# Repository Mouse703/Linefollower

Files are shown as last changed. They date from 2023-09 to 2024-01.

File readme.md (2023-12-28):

# LineFollower Louis Van Roosmaelen

Plan A

## Specifications

**Microcontroller:** ESP32-WROOM NodeMCU (CP2102)

**Motors:** 2x 6VDC Motors 50:1 micro metal gearbox

**H-Bridge:** DollaTek DRV8833

**Sensors:** Pololu QTR-8A

**Batteries:** 2x XTAR 18650 (2200mAh, 5A, protected)

**Wireless Communication:** Telnet communication over WiFi (with optional web server)

**Distance Sensor - Motors:**
- Plan A: 107.5mm
- Plan B: 80mm

**Weight:**
- Plan A: 249 grams
- Plan B: 364 grams

**Speed:**
- Plan A: 0.633m/s
- Plan B: 0.446m/s

Plan A

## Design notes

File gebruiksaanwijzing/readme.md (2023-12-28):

# Gebruiksaanwijzing

## Opladen / Vervangen Batterijen
Het opladen van de batterijen gebeurt met de XTAR MC2 Plus lader. Plaats de batterijen in de houder met de juiste polariteit. Verbind de lader met je PC via een USB-kabel. Wanneer de 4 blauwe streepjes constant branden, zijn de batterijen opgeladen. Je kunt dit ook controleren met een multimeter; de volledig opgeladen spanning is 4,18V.

## Draadloze Communicatie
### Verbinding maken
Verbinding met de robot gebeurt via Telnet over WiFi. In het `config.h` bestand dien je de SSID en het wachtwoord van je netwerk in te vullen, alsook kan je best een hostname instellen voor je robot. Het WiFi netwerk kan zowel een thuisnetwerk als een hotspot zijn, maar het netwerk moet de 2.4GHz band ondersteunen. Dit komt omdat de ESP-32 van de robot alleen op 2.4GHz werkt. Ook moet je ervoor zorgen dat je op hetzelfde WiFi netwerk zit. Wanneer dit is ingevuld kan je de code uploaden naar de ESP-32 (zie handleiding).

Als je de robot met je PC wilt verbinden, hoef je geen extra software te installeren. Wel moet je een Windows-functie inschakelen door naar "Turn Windows features on or off" te gaan. Hier vind je de Telnet Client, die je moet aanvinken zodat de benodigde functies worden geïnstalleerd. 

Het ip adres kan je vinden door met een powershell terminal of command prompt een ping command te sturen. Dit kan gedaan worden met `ping -4 robot` (met robot als gekozen hostname) Je kan ook het ip address vinden in je hotspot-instellingen of door een USB-verbinding met de robot te maken en de seriële monitor te openen. Deze toont dan het IP adress / telnet poort waarmee de robot kan verbonden worden.

### 1: Powershell terminal (PC)
1. Zet de hotspot aan of verbind met hetzelfde WiFi-netwerk waar de ESP-32 zich op bevindt.
2. Open een powershell terminal met de toetsencombinatie `WIN` + `X` en selecteer Terminal.
3. Voer het commando telnet in met uw IP of hostname gevolgd door de telnet poort (bvb `telnet 192.168.137.239 2121`)
4. Nu wordt er automatisch een nieuwe window geopend en kan u commando's ingeven.

### 2: Mobile Telnet (smartphone app)
1. Zet de hotspot aan of verbind met hetzelfde WiFi-netwerk waar de ESP-32 zich op bevindt.
2. Open de app en klik rechtsboven op de 3 puntjes
3. Klik op telnet settings en voer het juiste IP address in met de bijhorende poort
4. Klik op connect en nu kan u commando's ingeven.

### Commando's
- `debug` Toont alle instelbare parameters
- `run (start/stop)` Start of stopt de robot
- `set cycle [µs]` Stelt de cyclustijd van de ESP-32 in
- `set power [0..255]` Stelt de kracht van de motoren in
- `set diff [0..1]` Stelt in hoe hard de robot moet bijsturen in de bochten (0 niets, 1 veel)
- `set kp [0..]` Stelt de proportionele correctie van de fout in (P-regeling)
- `set ki [0..]` Stelt de integrerende correctie van de fout in (I-regeling)
- `set kd [0..]` Stelt de differentiële correctie van de fout in (D-regeling)
- `set ledon` Zet de voor- en achterlichten aan
- `set ledred [0..255]` Stelt de helderheid van de rode lichten in
- `set ledorange [0..255]` Stelt de helderheid van de oranje lichten in
- `set ledwhite [0..255]` Stelt de helderheid van de witte lichten in
- `set ledstatus [0..255]` Stelt de helderheid van de statuslichten in
- `calibrate black` Kalibreert de zwartwaarden
- `calibrate white` Kalibreert de witwaarden

## Kalibratie
Kalibreer de zwartwaarden door de robot op een zwart oppervlak van het circuit te plaatsen en voer vervolgens het commando `calibrate black` in. Herhaal dit proces voor de witwaarden door de robot op een wit oppervlak van het circuit te plaatsen en het commando `calibrate white` in te voeren.

## Instellingen
De robot rijdt stabiel met de volgende parameters:
- **Cycle time**: 2500
- **Power**: 100
- **Diff**: 0.05
- **Kp**: 5
- **Ki**: 0
- **Kd**: 0

## Start/Stop-knop
De start/stop-knop bevindt zich naast de blauwe status-LED. Druk op deze knop om de running state van de robot te wijzigen, wat betekent dat de robot zal beginnen met rijden of stoppen, afhankelijk van de huidige toestand.

## Status LED's
Op de PCB bevinden zich status LED's. De brightness hiervan wordt ingesteld met `set ledstatus [0..255]`. De functie van deze LED's staan hieronder uitgelegd.
- **Blauwe LED** Bij knipperen: er wordt poging gedaan om met WiFi te verbinden. Bij vast licht: er is verbinding met een WiFi client. Bij geen licht: de WiFi verbinding is verbroken, robot moet herstart worden indien er weer parameters moeten aangepast worden.
- **Groene LED** Bij vast licht: de robot is klaar om te rijden maar in standby modus, er is een run command nodig of een druk op de startknop.
- **Oranje LED** Bij vast licht: de robot is aan het rijden.
- **Rode LED** Bij vast licht: de robot is buiten het parcour gegaan, er is een nieuwe run command nodig of een druk op de startknop.

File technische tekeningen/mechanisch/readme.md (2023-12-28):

# Mechanische Tekeningen

Dit is de verzameling mechanische tekeningen van het ontwerp, gemaakt met **Autodesk Inventor Professional 2024**. Hieronder vindt je ook de bronnen van alle geïmporteerde CAD modellen.

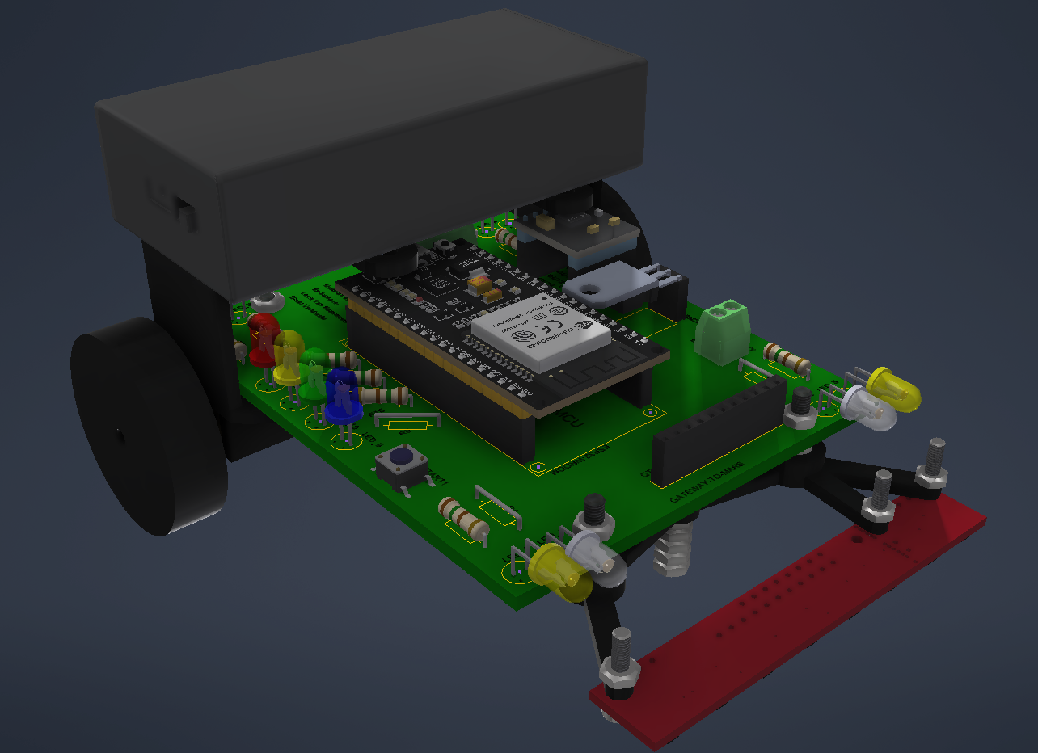
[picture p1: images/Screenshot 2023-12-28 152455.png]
3D Model - Plan A


## Source Imported CAD Files:

1. **Battery Holder 18650**
   - [Bekijk op GrabCAD](https://grabcad.com/library/3-7v-18650-2s-holder-1)

2. **DC Motor**
   - [Bekijk op GrabCAD](https://grabcad.com/library/dc-micro-metal-gearmotor-1)

3. **DRV 8833**
   - [Bekijk op GrabCAD](https://grabcad.com/library/drv8833-carrier-breakout-board-1)

4. **ESP32-WROOM-32S**
   - [Bekijk op GrabCAD](https://grabcad.com/library/esp32-wroom-32s-nodemcu-32s-1)

5. **Female Headers**
   - [Bekijk op GrabCAD](https://grabcad.com/library/arduino-female-pin-header-for-kicad-1)

6. **L7805CV**
   - [Bekijk op GrabCAD](https://grabcad.com/library/l7805-with-heat-sink-1)

7. **LED 5mm**
   - [Bekijk op GrabCAD](https://grabcad.com/library/led-5mm-0-2-inch-1)

8. **Pushbutton**
   - [Bekijk op GrabCAD](https://grabcad.com/library/pushbutton-switch-1)

9. **QTR-8A Reflectance Sensor Array**
   - [Bekijk op GrabCAD](https://grabcad.com/library/qtr-8a-reflectance-sensor-array-1)

10. **Resistor**
    - [Bekijk op GrabCAD](https://grabcad.com/library/resistors-0-5w-pitch-12-7mm-500mil-1)

11. **Screw Terminal**
    - [Bekijk op GrabCAD](https://grabcad.com/library/pcb-terminal-block-pitch-3-5mm-for-kicad-1)

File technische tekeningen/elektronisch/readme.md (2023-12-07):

# Electrical schematics

Schematics for plan A (using PCB) and plan B (using breadboard)

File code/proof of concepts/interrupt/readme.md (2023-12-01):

# Start/stop interrupt proof of concept
minimale hard- en software die de correcte werking van een start/stop drukknop aantoont, gebruik makend van een hardware interrupt

Interrupt_bb

ESP-32 WROOM used from:
https://github.com/Warlib1975/Fritzing-parts/blob/master/MH-ET%20LIVE%20ESP32%20DEVKIT%2038%20pins.fzpz

Interrupt_schem

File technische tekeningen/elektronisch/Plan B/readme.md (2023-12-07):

# Plan B - Breadboard
Plan B is the test phase of the line follower, everything gets mounted on a breadboard for easy testing. When test phase is complete plan A will be used.

Plan B - Schema_bb

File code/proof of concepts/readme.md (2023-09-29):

# Proof of Concepts

Een proof of concept is een combinatie van minimale hard- en software om eenvoudig aan te tonen dat iets werkt.  
Proof of concepts kunnen enerzijds als eerste poging dienen om een bepaald onderdeel van het project werkend te krijgen. Anderzijds kunnen ze tijdens het debuggen van het finale project dienen als test om eventuele hardware problemen te elimineren bij onduidelijke problemen.
<br />  
<br />
Een proof of concept bestaat uit
* een elektronisch schema (indien van toepassing)
* minimale code om de voorop gestelde zaken te demonstreren
* minimale uitleg / aandachtspunten
<br />
De elektronische schakelingen van de proof of concepts komen bij voorkeur overeen met deze van de uiteindelijke linefollower, zodat de code zonder aanpassingen op het finale project kan draaien.

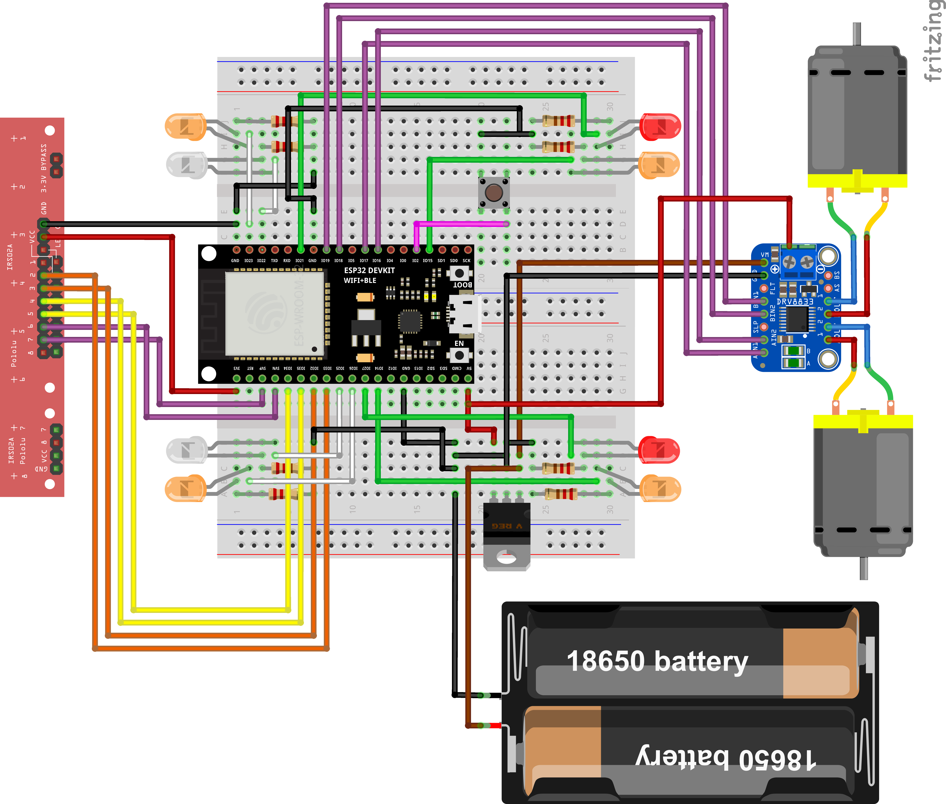
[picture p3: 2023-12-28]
technische tekeningen/mechanisch/Workingfolder - ELM3 - Project Synthese - LFR/Documents/Fritzing/Exports/Plan B - Schema_bb.png

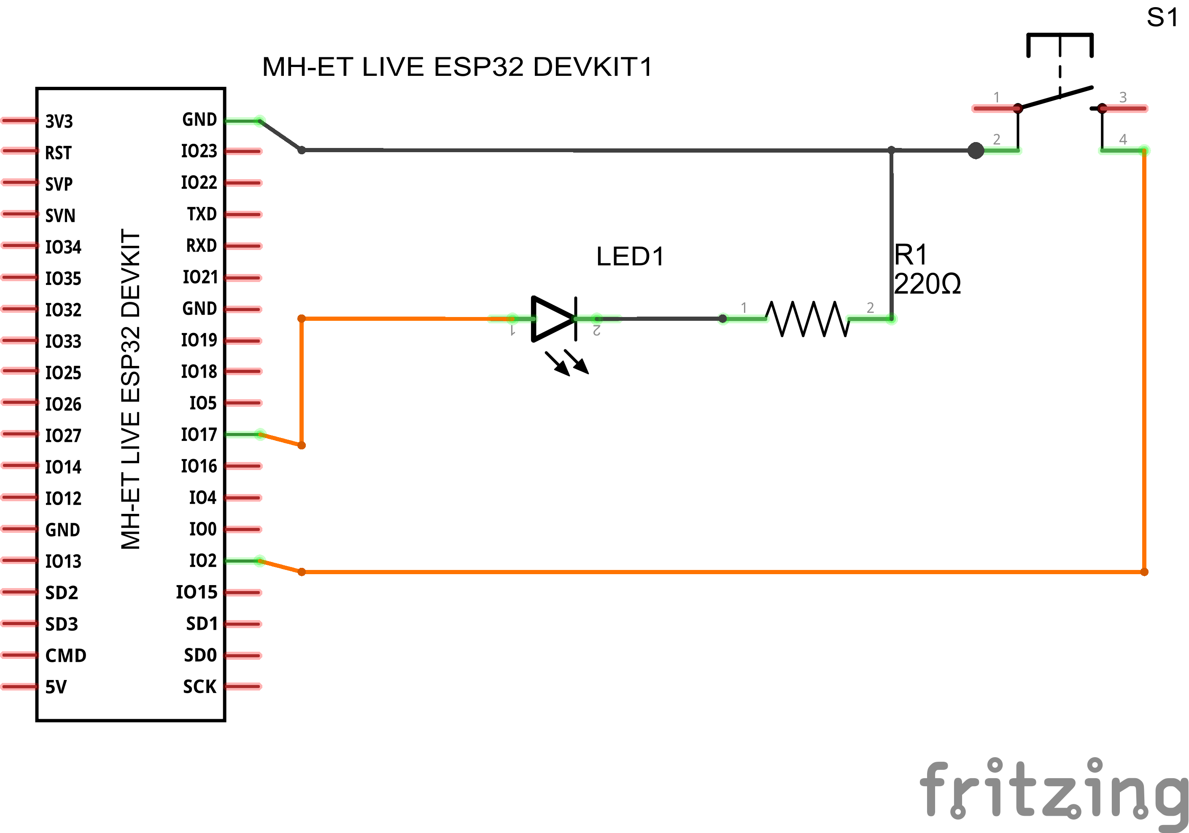
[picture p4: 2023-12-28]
technische tekeningen/mechanisch/Workingfolder - ELM3 - Project Synthese - LFR/Documents/Fritzing/Exports/Interrupt_schem.png

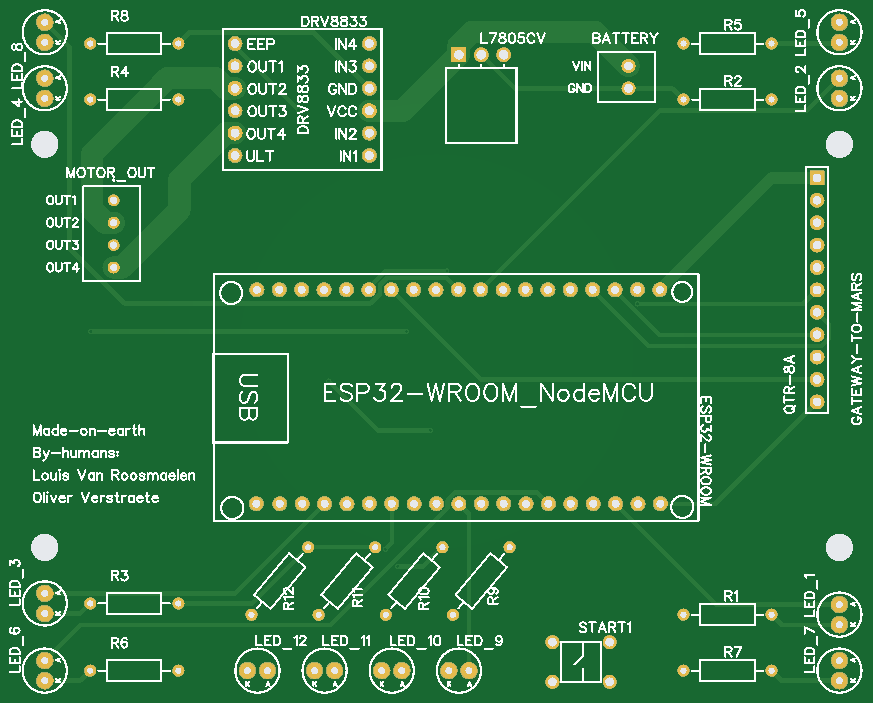
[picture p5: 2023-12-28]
technische tekeningen/mechanisch/Workingfolder - ELM3 - Project Synthese - LFR/Documents/PCB/PCB Preview.png

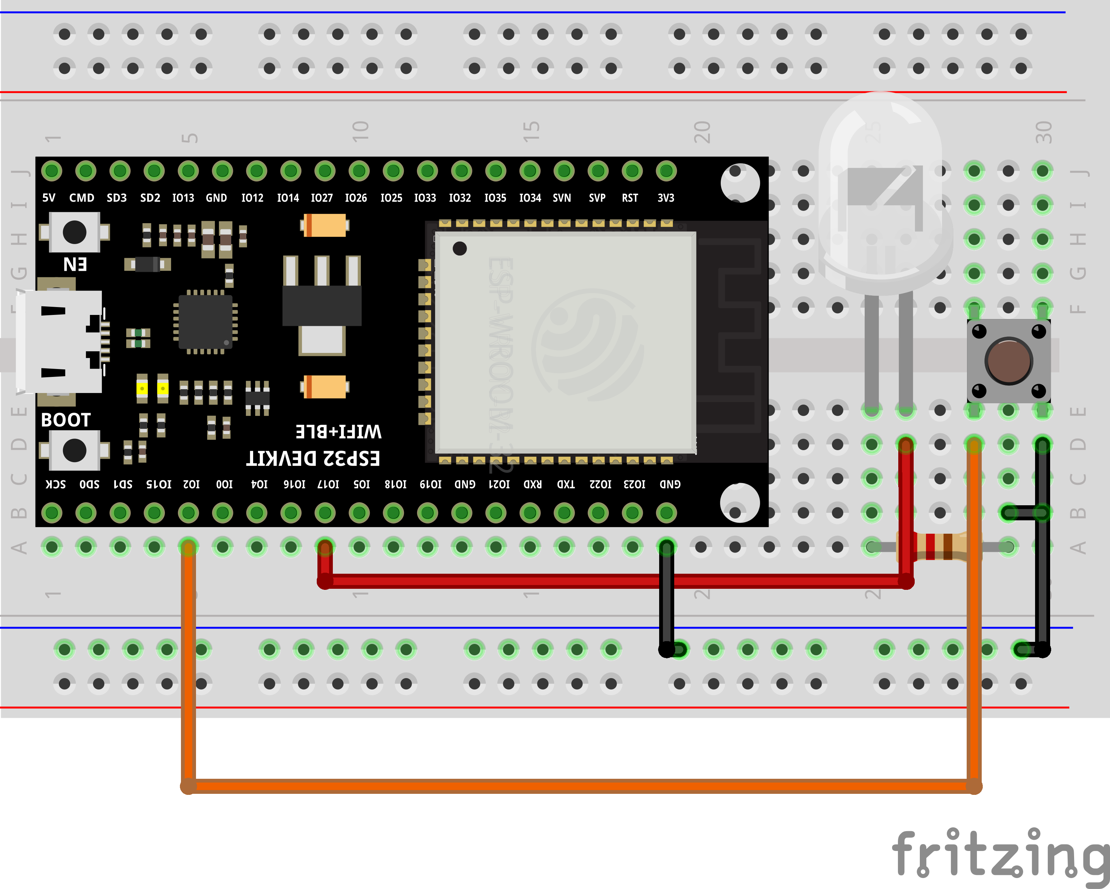
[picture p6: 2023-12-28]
technische tekeningen/mechanisch/Workingfolder - ELM3 - Project Synthese - LFR/Documents/Fritzing/Exports/Interrupt_bb.png

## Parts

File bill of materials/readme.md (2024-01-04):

## Bill of materials
<br />

|Volgnummer|Naam |Omschrijving |Nieuw/recup |Kostprijs/stuk|Aantal|Shipping|Subtotaal|
|---|---|---|---|---|---|---|---|
| 1| PA_Main |Behuizing (0,20mm NORMAL) |Ge-3D-print, Ender-3 V2 |0.93 |1 |0 |0.93 |
| 2| PA_Sensor |Vaste houder sensor 107.5mm (0,08mm SUPERDETAIL) |Ge-3D-print, Ender-3 V2 |0.05 |1 |0 |0.64 |
| 3| Pololu DC Micro Metal Gear 12V |50:1 ratio, 12VDC |Nieuw |10.56 |2 |9.99 |31.11 |
| 4| Batteries XTAR |XTAR 18650 (2200mAh, 5A, protected) |Nieuw |4.45 |2 |3.21 |12.11 |
| 5| Battery charger |XTAR MC1 Li-ion mini batterijlader |Nieuw |6.95 |1 |3.21 |10.16 |
| 6| Battery holder |2x18650 Batterijhouder met losse draden |Nieuw |0.96 |1 |1.46 |2.42 |
| 7| H-Bridge |DollaTek DRV8833 |Nieuw |1.90 |2 |1.46 |3.36 |
| 8| Reflectance sensor array |Polollulu QTR-8A |Nieuw |10.39 |1 |13.78 |24.17 |
| 9| Microcontroller ESP-32 |AZDelivery ESP32-WROOM-32 NodeMCU |Nieuw |7.60 |1 |0 |7.60 |
| 10| Wheels 40mm |Simulation rubber wheels 40mm |Nieuw |0.79 |2 |3.25 |4.04 |
| 11| PCB |PCB (aankoop min 5 stuks, taxen bij shipping) |Nieuw |1.11 |1 |22.03 |25.23 |
| 12| Tiny Tronics - PCB Component |4 Pin Schroef Terminal Block Connector 2.54mm |Nieuw |0.45 |1 |0 |0.45 |
| 13| Tiny Tronics - PCB Component |2 Pin Schroef Terminal Block Connector 2.54mm |Nieuw |0.30 |1 |0 |0.30 |
| 14| Tiny Tronics - PCB Component |20 Pins header Female |Nieuw |0.36 |2 |0 |0.72 |
| 15| Tiny Tronics - PCB Component |12 Pins header Female |Nieuw |0.28 |1 |0 |0.28 |
| 16| Tiny Tronics - PCB Component |6 Pins header Female |Nieuw |0.18 |2 |0 |0.36 |
| 17| Tiny Tronics - PCB Component |3 Pins header Female |Nieuw |0.12 |1 |0 |0.12 |
| 18| Tiny Tronics - PCB Component |6 Pins header Female |Nieuw |0.18 |2 |0 |0.36 |
| 19| Tiny Tronics - PCB Component |LED set 5mm - Groen - Rood - Geel - Blauw - Wit |Nieuw |3.00 |1 |0 |3.00 |
| 20| Tiny Tronics - PCB Component |10Ω-1MΩ Weerstanden Set |Nieuw |5.00 |1 |0 |5.00 |
| 21| Tiny Tronics - Shipping |Shipping |Nieuw |x |1 |7.95 |7.95 |
| 22| Countersunck crosshead screw |M3x12 |recup |x |9 |x |x |
| 23| DIN 912 |M2.5x18 |recup |x |3 |x |x |
| 24| DIN 985 |M2.5 |recup |x |3 |x |x |
| 25| Multi colour wires |0,75mm copper core wires |recup |x |x |x |x |
| 26| Pushbutton |Drukknop |recup |x |x |x |x |

Totaal zonder shipping: €73.69 

Totaal met shipping: €140.03

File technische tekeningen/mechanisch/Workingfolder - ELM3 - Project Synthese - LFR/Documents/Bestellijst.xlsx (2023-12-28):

Benodigdheden syntheseproject | Louis + Oliver + Roman
Onderdeel |  | Aantal | EPrijs | Kprijs | Verzending/BTW | Link
Motor | 50:1 Micro metal gearbox HP 6V | 6.00 | 2.04 | 12.24 | 3.22 | https://nl.aliexpress.com/item/33022320164.html?mp=1
Batterijen | XTAR 18650 2200mAh (protected) - 5A | 6.00 | 4.45 | 26.70 | 6.41 | https://www.nkon.nl/xtar-18650-2200mah-li-ion-battery.html
Batterijen oplader | XTAR MC1 Li-ion mini batterijlader | 3.00 | 6.95 | 20.85 | 0.00 | https://www.nkon.nl/charger-75/battery-charger/li-ion/xtar-mc2-plus-batterijlader.html
Batterijhouder | 2x 18650 Batterijhouder met losse draden | 3.00 | 0.32 | 0.96 | 2.92 | https://nl.aliexpress.com/item/32832812448.html?mp=1
H-brug | DollaTek 5 x DRV8833 | 1.00 | 5.47 | 5.47 | 0.00 | https://nl.aliexpress.com/item/1005006025943342.html?curPageLogUid=GeaIyxtrKBlw
Sensoren | QTR-8A Reflectance Sensor | 3.00 | 10.39 | 31.17 | 13.78 | https://www.melopero.com/shop/sensori/qtr8areflectancesensorarray/
Draadloze communicatie | Included (WiFi/Bluetooth) | 0.00 | 0.00 | 0.00 | 0.00 | n.v.t.
Microcontroller | AZDelivery ESP32 NodeMCU | 3.00 | 7.60 | 22.79 | 0.00 | https://www.amazon.com.be/-/nl/dp/B074RG86SR?psc=1&ref=ppx_yo2ov_dt_b_product_details
Wielen | Rubber wheel 40mm | 3.00 | 3.15 | 9.45 | 3.25 | https://nl.aliexpress.com/item/1005001687355617.html?curPageLogUid=2HmPvmFUd0g8
Breadboard | Breadbord 400mm | 6.00 | 1.02 | 6.12 | 5.03 | https://nl.aliexpress.com/item/32711841420.html?curPageLogUid=Gr2BDQawu44Q
Prijs totaal zonder shipping |  |  |  | 135.75
Totale shippingkosten en/of BTW |  |  |  | 34.61
Totale prijs |  |  |  | 170.36
Prijs per persoon (incl. shipping) |  |  |  | 56.79

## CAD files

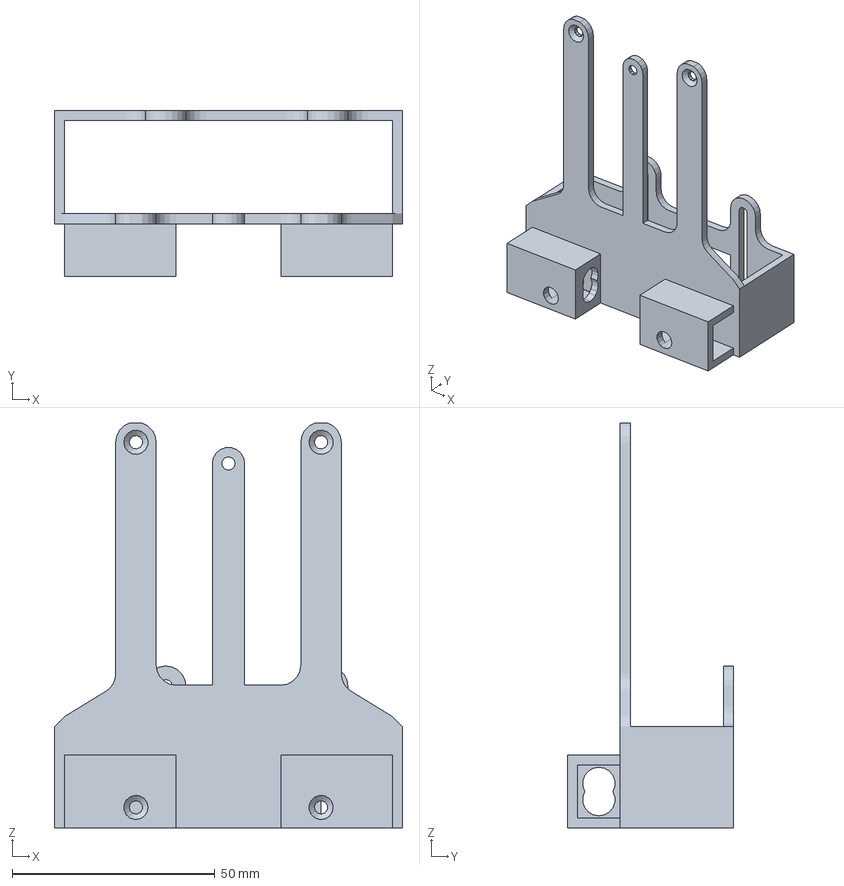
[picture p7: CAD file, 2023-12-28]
technische tekeningen/mechanisch/Workingfolder - ELM3 - Project Synthese - LFR/Engineering Data/PrusaSlicer/PA_Main.3mf
86.0 x 41.0 x 100.0 mm

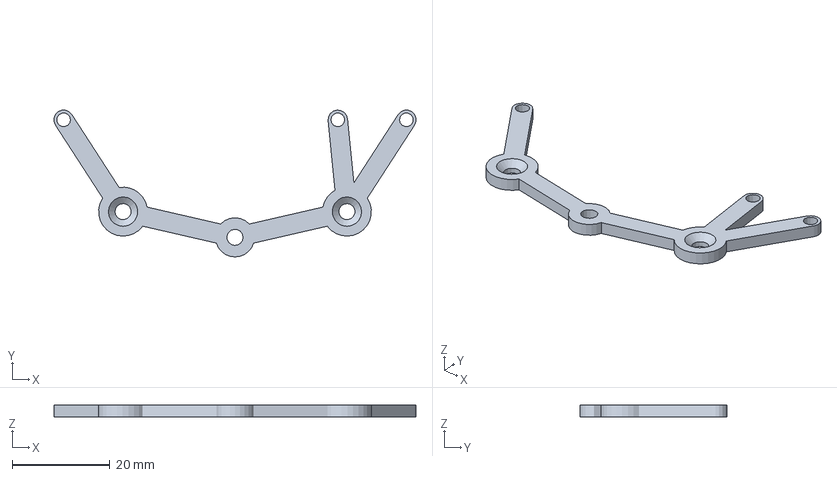
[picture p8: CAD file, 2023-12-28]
technische tekeningen/mechanisch/Workingfolder - ELM3 - Project Synthese - LFR/Engineering Data/PrusaSlicer/PA_Sensor.3mf
73.9 x 30.0 x 2.40 mm

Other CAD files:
technische tekeningen/mechanisch/Workingfolder - ELM3 - Project Synthese - LFR/Engineering Data/STL/PA_Main.stl
technische tekeningen/mechanisch/Workingfolder - ELM3 - Project Synthese - LFR/Engineering Data/STL/PA_Sensor.stl
technische tekeningen/mechanisch/Workingfolder - ELM3 - Project Synthese - LFR/Content Center/en-US/DIN 125-1 A/DIN 125 - A 4.3.ipt
technische tekeningen/mechanisch/Workingfolder - ELM3 - Project Synthese - LFR/Content Center/en-US/DIN 912/DIN 912 - M2.5 x 0.45 x 12 x 10.875.ipt
technische tekeningen/mechanisch/Workingfolder - ELM3 - Project Synthese - LFR/Content Center/en-US/DIN 912/DIN 912 - M4 x 0.7 x 16 x 14.25.ipt
technische tekeningen/mechanisch/Workingfolder - ELM3 - Project Synthese - LFR/Content Center/en-US/DIN 912/DIN 912 - M4 x 0.7 x 20 x 18.25.ipt
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

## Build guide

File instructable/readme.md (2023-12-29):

# Instructible

## Inhoudsopgave
1. [Bestellen van Componenten](#stap-1-bestellen-van-componenten)
2. [3D-printen](#stap-2-3d-printen)
3. [Tools en Overzicht](#stap-3-tools-en-overzicht)
4. [Elektrische Montage op PCB (Headers)](#stap-4-elektrische-montage-op-pcb-headers)
5. [Elektrische Montage op PCB (Weerstanden)](#stap-5-elektrische-montage-op-pcb-weerstanden)
6. [Elektrische Montage op PCB (LED’s)](#stap-6-elektrische-montage-op-pcb-leds)
7. [Montage Sensorhouder op het Chassis](#stap-7-montage-sensorhouder-op-het-chassis)
8. [Monteren PCB op het Chassis](#stap-8-monteren-pcb-op-het-chassis)
9. [Elektrische Montage QTR-8A](#stap-9-elektrische-montage-qtr-8a)
10. [Monteren QTR-8A op Chassis en Verbinding met PCB](#stap-10-monteren-qtr-8a-op-chassis-en-verbinding-met-pcb)
11. [Monteren van de Motoren](#stap-11-monteren-van-de-motoren)
12. [Monteren Batterijhouder en Spanningsverdeler](#stap-12-monteren-batterijhouder-en-spanningsverdeler)
13. [Installeren Visual Studio Code](#stap-13-installeren-visual-studio-code)
14. [Installeren Platform.io](#stap-14-installeren-platformio)
15. [Openen project](#stap-15-openen-project)
16. [Installeren driver voor ESP32](#stap-16-installeren-driver-voor-esp32)
17. [Parameters UserConfig.h](#stap-17-parameters-userconfigh)
18. [Uploaden naar ESP32](#stap-18-uploaden-naar-esp32)
19. [Batterijen plaatsen](#stap-19-batterijen-plaatsen)
20. [Robot starten](#stap-20-robot-starten)

---

## Stap 1: Bestellen van Componenten
In de [Bill of Materials](../bill%20of%20materials) (BOM) vindt u de benodigde componenten, die verkrijgbaar zijn bij de bijbehorende link. Als de link niet meer werkt, kunt u altijd ook een vervangende zoeken op Amazon of AliExpress. Het is handig om van elk onderdeel ten minste twee exemplaren te kopen, waardoor u bij eventuele defecten direct een vervangend exemplaar paraat heeft.

## Stap 2: 3D-printen
Er zijn diverse methoden beschikbaar om de onderdelen te 3D printen. Indien u in het bezit bent van een Ender-3 V2, kunt u eenvoudig de [.gcode](../technische%20tekeningen/mechanisch/GCODE) bestanden uploaden naar een SD-kaart en direct aan de slag gaan met printen (gebruikmakend van PLA, extruder ingesteld op 200°C en het printbed op 60°C). Wil je de printerinstellingen nakijken of aanpassen, dan kunt u de [.3mf](../technische%20tekeningen/mechanisch/PrusaSlicer) bestanden openen in PrusaSlicer. Voor degenen die de voorkeur geven aan andere software, is het ook mogelijk om de [.stl](../technische%20tekeningen/mechanisch/STL) bestanden te importeren. Als u wijzigingen wilt aanbrengen in het 3D-design, kunt u de originele [originele bestanden](../technische%20tekeningen/mechanisch/Workingfolder%20-%20ELM3%20-%20Project%20Synthese%20-%20LFR) openen met Autodesk Inventor. Het is van belang om alles te downloaden binnen deze map, zodat Inventor alle benodigde referenties kan vinden.

## Stap 3: Tools en Overzicht
Zorg voor een workspace dat goed en gestructureerd is, dit voorkomt het verliezen van componenten. Voor tools hebt u het volgende nodig:
1. Toolbox met inbussleutels, dopsleutels en schroevendraaiers.
2. Een kniptang en striptang.
3. Breekmes, schuifmaat en dubbelzijdige plakband zijn ook handig.
4. Soldeerstation met de bijbehorende tin.

## Stap 4: Elektrische Montage op PCB (Headers)
Neem de volgende componenten erbij:
- PCB
- 1x 2-pin schroef terminal block
- 1x 4-pin schroef terminal block
- 1x 3-pin header female
- 2x 6-pin header female
- 1x 12-pin header female
- 2x 20-pin header female

We knippen van de 20 pin female headers 1 pin eraf zodat dit een 19 pin header wordt, deze past dan in de PCB. Vervolgens doen we hetzelfde voor de 12 pin female header, zodat deze een 11 pin header wordt. Soldeer nu de componenten aan de PCB zoals te zien op onderstaande foto.



## Stap 5: Elektrische Montage op PCB (Weerstanden)
Neem nu 9 weerstanden van 150Ω. Soldeer deze op de aangegeven locaties op het PCB, namelijk R3, R4, R5, R6, R7, R8, R10, R11 en R12. Voor R1, R2 en R9 hoeft geen weerstand te worden geplaatst; in plaats daarvan kan je restanten van andere gebruiken om de weerstanden te overbruggen. Dit komt doordat de blauwe en witte LED's, volgens de informatie op de website van de verkoper (TinyTronics), geen voorschakelweerstand nodig hebben. Als u andere LED's hebt gekocht, is het mogelijk dat ze wel een voorschakelweerstand nodig hebben, en in dat geval kunt u deze op die posities plaatsen.



## Stap 6: Elektrische Montage op PCB (LED’s)
Neem nu de volgende componenten erbij:
- 1x blauwe LED
- 1x groene LED
- 2x witte LED’s
- 3x rode LED’s
- Pushbutton
- ESP32-WROOM-32
- DRV8833

Soldeer de LED’s op de juiste plaats. Soldeer witte LED’s op LED_1 en LED_2. Voor LED_3, LED_4 en LED_12 soldeer je rode LED's. Op LED_5, LED_6, LED_7, LED_8 en LED_11 soldeer je oranje LED's. Op LED_10 komt een groene LED en ten slotte op LED_9 soldeer je een blauwe LED. Neem een pushbutton erbij en soldeer deze op de aangewezen plaats genaamd START1. Vervolgens nemen we de DRV8833 en solderen we de male headers met de korte pinnen aan de bovenkant zoals op de foto te zien is. Ten slotte plaatsen we de ESP-32 op de headers met de usb poort naar de achterkant, zoals het diagram op de PCB aantoont.



## Stap 7: Montage Sensorhouder op het Chassis
Neem het ge-3d-printe chassis en de ge-3d-printe sensorhouder. Deze worden verbonden met elkaar door middel van M3x16 en M3x10 bouten. Plaats de bouten zoals op de foto en bevestig de moeren. De twee achterste bouten bij de motor moeten M3x10 zijn, terwijl de drie voorste bouten bij de sensorhouder M3x16 moeten zijn.



## Stap 8: Monteren PCB op het Chassis
Neem het chassis en plaats de PCB over de 4 bouten die naar boven uitsteken. Neem dan 4 bouten en bevestig de PCB aan het chassis.



## Stap 9: Elektrische Montage QTR-8A
Neem de volgende componenten erbij:
- QTR-8A
- Krimpkous (⌀2,5)
- Kabels vaste kern (0,8mm²)

Neem de QTR-8A sensor en soldeer de mannelijke headers op de sensor volgens de afbeelding. Vervolgens gebruik je enkele kabels van ongeveer 6 cm. Soldeer deze kabels aan de mannelijke headers en schuif de krimpkous over de kabels, zoals te zien is op de foto. Verwarm ten slotte de krimpkous met een haardroger of lucifer.

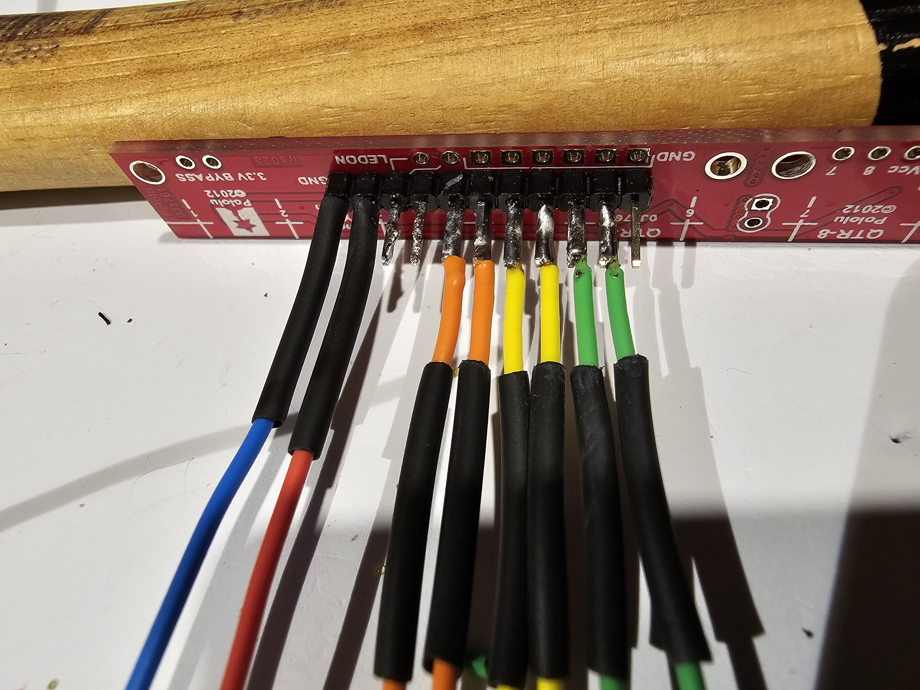
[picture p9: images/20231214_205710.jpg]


## Stap 10: Monteren QTR-8A op Chassis en Verbinding met PCB
Bevestig de QTR-8A sensor aan het chassis volgens de afbeelding. Hiervoor zijn 3 M2,5x12 bouten en 3 M2,5 moeren nodig. Zodra de sensor is bevestigd, kunt u de draden aansluiten zoals aangegeven door de paden op de PCB. De GND bevindt zich helemaal links, terwijl de VCC helemaal rechts bij de bout zit. Als je niet zeker bent, kun je de traces op de PCB volgen om te zien waar ze naartoe leiden.



## Stap 11: Monteren van de Motoren
Neem de twee DC-motoren en voorzie ze elk van twee kabels: een rode voor de positieve zijde (+) en een blauwe voor de negatieve zijde (-). Plaats vervolgens de motoren met de kabels eerst in de houder. Bevestig da

## Stap 12: Monteren Batterijhouder en Spanningsverdeler
Neem de volgende componenten erbij:
- Batterijhouder
- 2x M3x10 bouten
- 2x M3 moeren
- 2x kabels vaste kern (0,8mm²)
- Krimpkous
- Spanningsverdeler (L7805CV)

Eerst gaan we de uiteinden van de batterijhouder voorzien van een draad met een vaste kern. Dit maakt het gemakkelijker om ze te verbinden met de schroefterminal van de PCB. Soldeer de rode draad van de batterijhouder aan een draad met een vaste kern en plaats er een stukje krimpkous over. Verwarm de krimpkous en herhaal dit proces voor de andere draad van de batterijhouder. Plaats vervolgens de draden in de juiste polariteit (bruin/rood naar VIN en zwart/blauw naar GND) in de schroefterminal. Bevestig de batterijhouder met M3-bouten en moeren zoals weergegeven in de foto. Ten slotte bevestigen we de spanningsverdeler (L7805CV) aan de PCB. Zorg ervoor dat de zijde met de heat spreader naar boven wijst, omdat de polariteit correct moet zijn. Bij twijfel kun je altijd de datasheet en het elektrisch schema raadplegen.



## Stap 13: Installeren Visual Studio Code
Om het correcte programma te uploaden naar onze ESP32 moeten we Visual Studio Code installeren. Dit kan heel simpel gedaan worden door een powershell terminal te openen en volgend commmando in te geven `winget install -e --id Microsoft.VisualStudioCode`

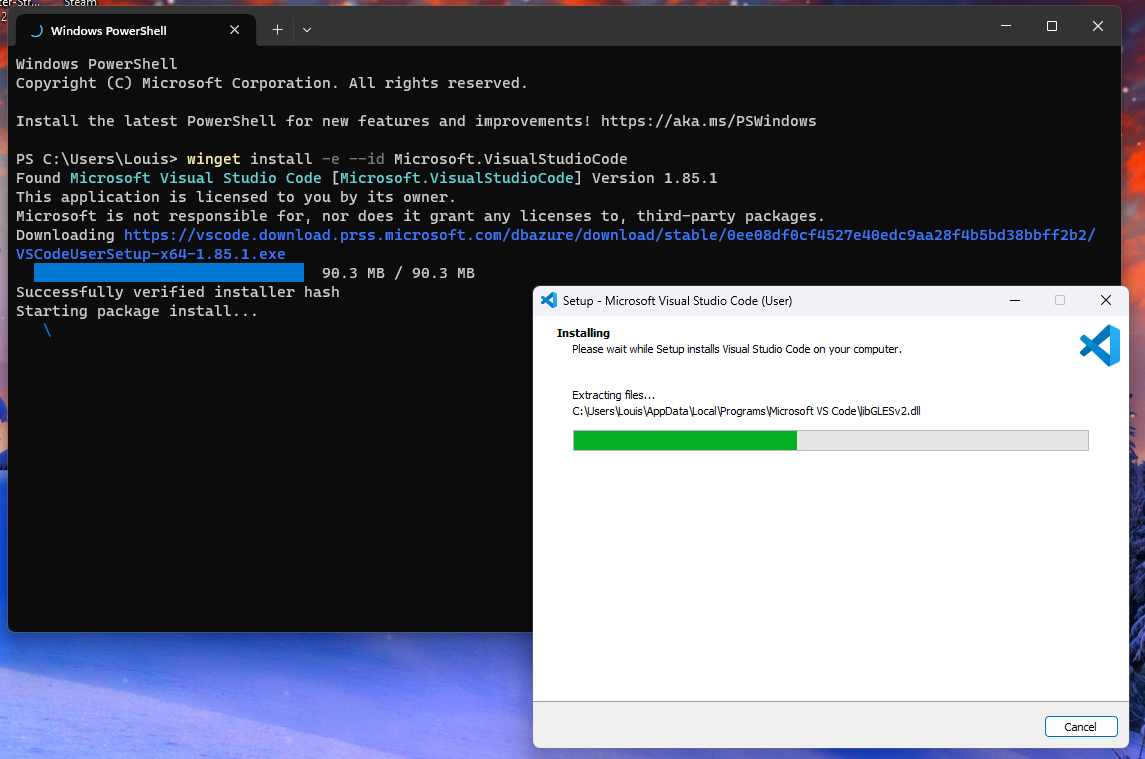
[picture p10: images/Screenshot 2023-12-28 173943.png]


## Stap 14: Installeren Platform.io
Nu moeten we een IDE installeren in Visual Studio zodat we gemakkelijk kunnen uploaden. Dit doen we door naar extensions te gaan in visual studio code, dan te zoeken naar PlatformIO IDE en deze te installeren.

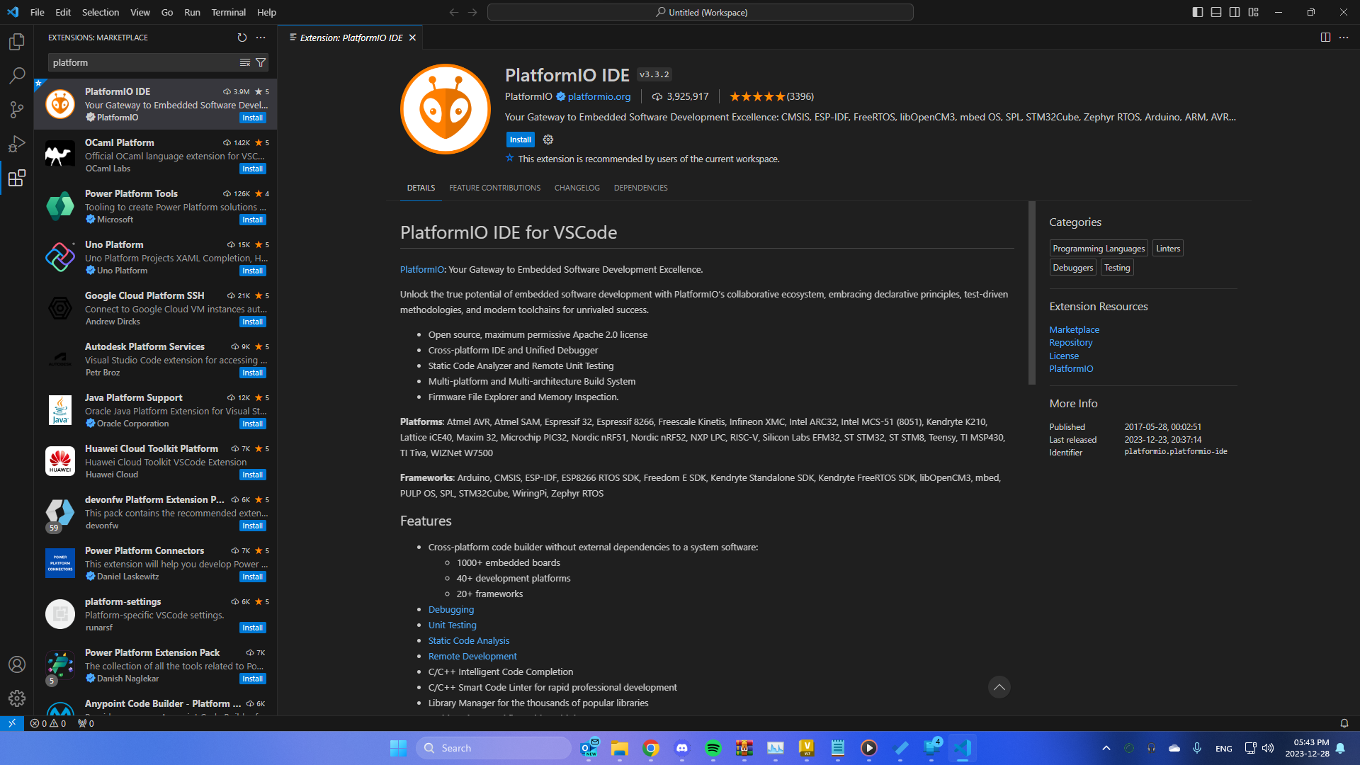
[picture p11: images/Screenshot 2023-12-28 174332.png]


## Stap 15: Openen project
Om het project te openen in platform.io gaan we naar PIO Home -> Open -> Open Project. [Het project vind je hier (download de map Syntheseproject - Code)](../code/finaal/) 

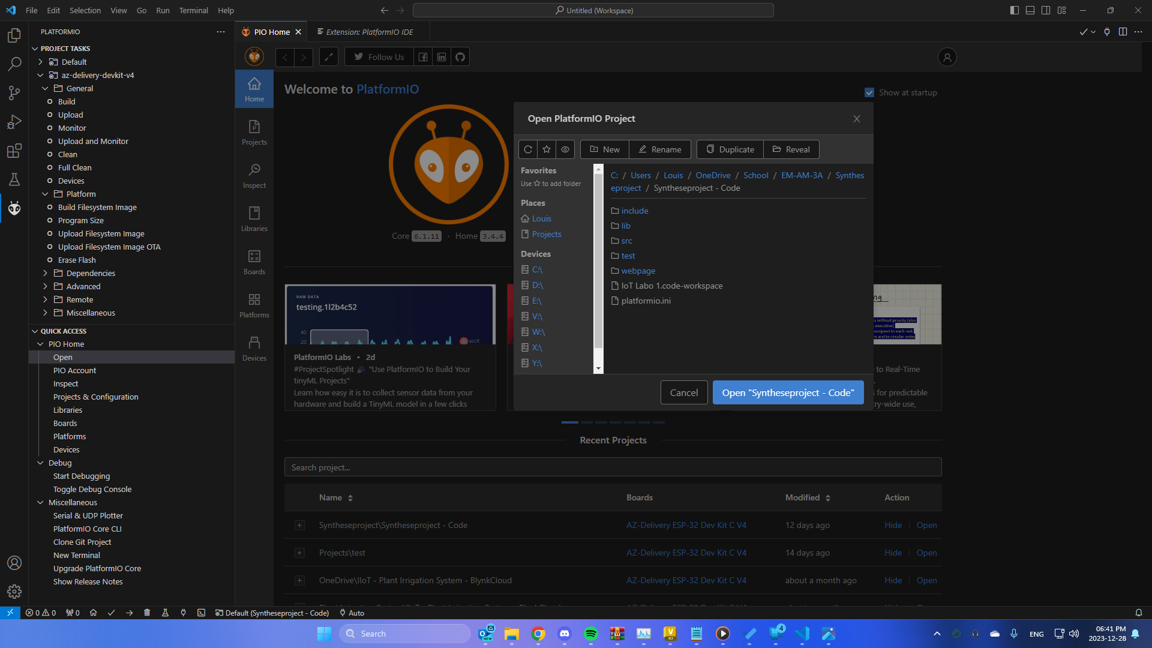
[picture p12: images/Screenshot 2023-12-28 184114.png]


## Stap 16: Installeren driver voor ESP32
Verbind nu de ESP32 met de computer, OPGELET, indien de batterijen van de robot al in de houder zitten dan moeten die UIT staan, als dit niet gedaan wordt zal je 8,4V op de USB poort terugsturen wat permanente schade kan toebrengen. De ESP32 zal nu nog niet herkend worden op de computer, eerst moeten we een driver installeren. [Deze driver (CP210x) je hier vinden.](../code/finaal/) Ga dan naar `apparaatbeheer` of `device manager` (te vinden in controlepaneel) op je computer. Bij `overige apparaten` of `other devices` zie je nu staan `CP2102 USB to UART Bridge Controller` met een warning sign. Rechtermuisklik op het apparaat en klik op update driver. Selecteer dan `Browse my computer for drivers` en ga naar de map waar je de CP210x driver hebt gedownload. Klik dan op next en dan op close wanneer alles geupdate is.

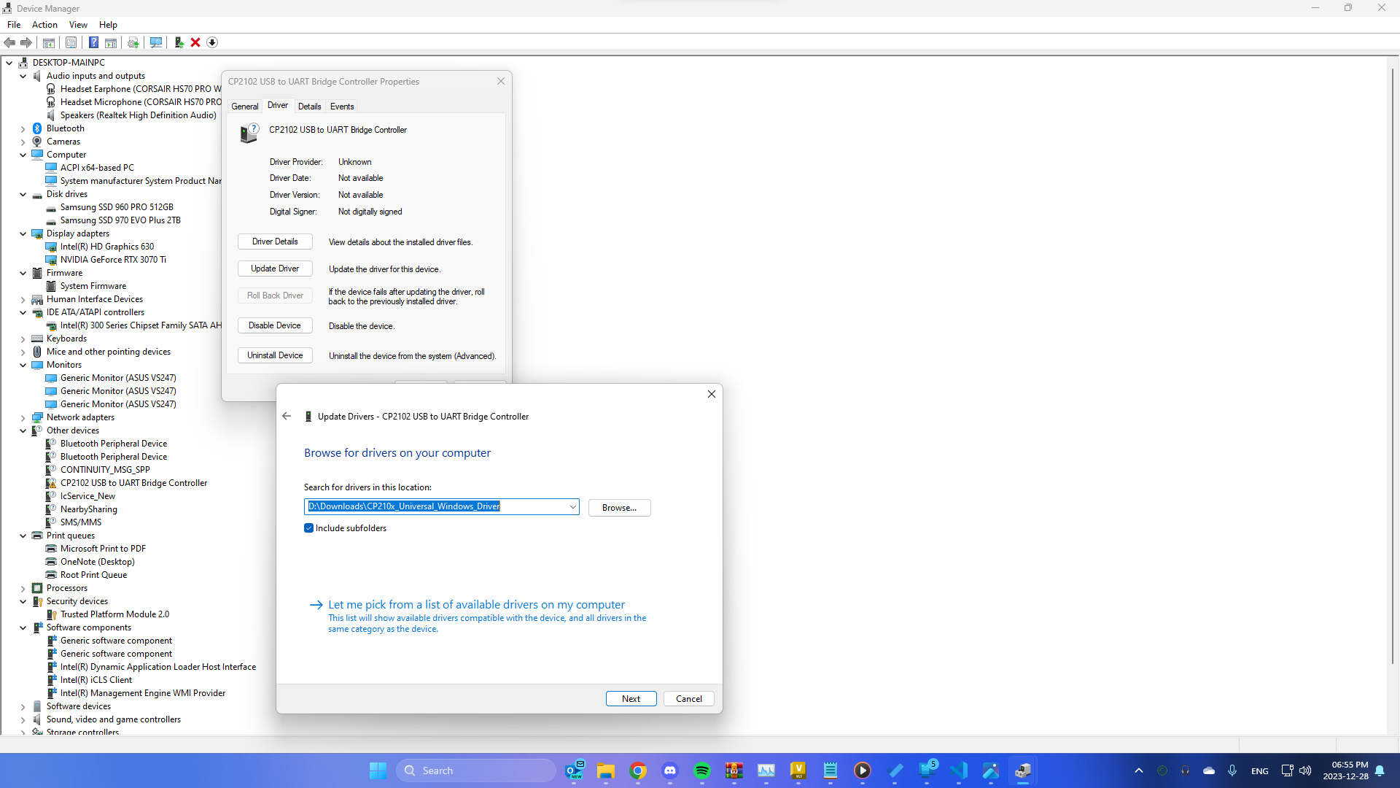
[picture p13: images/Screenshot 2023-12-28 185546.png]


## Stap 17: Parameters UserConfig.h
Ga nu terug naar Visual Studio. In de explorer van visualstudio klap je nu `src` open, daarin staan twee bestanden, `main.cpp` en `UserConfig.h`. Open `UserConfig.h` en stel uw eigen parameters in. `ssid` is de netwerknaam van uw netwerk, `pswd` is het passwoord van uw netwerk en `host` is om gemakkelijk uw device terug te vinden op uw netwerk.

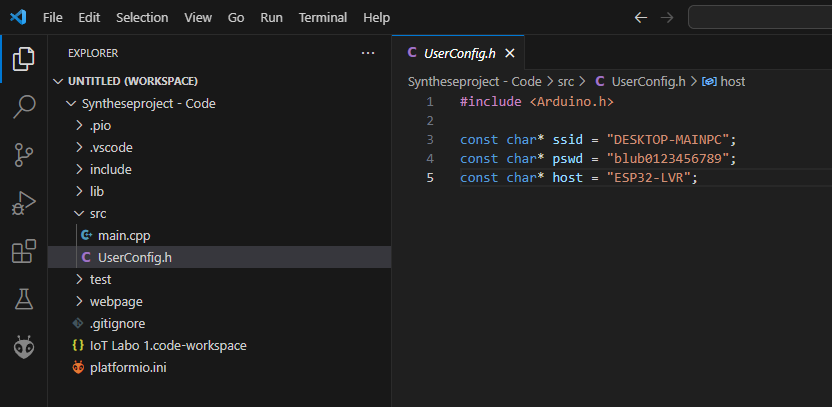
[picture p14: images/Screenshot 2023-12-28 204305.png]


## Stap 18: Uploaden naar ESP32
Klik nu op upload dat je kan vinden in de balk linksonder, het ziet eruit als een pijltje. Wanneer dit succesvol gedaan is zie je in de terminal `SUCCES` in het groen verschijnen.

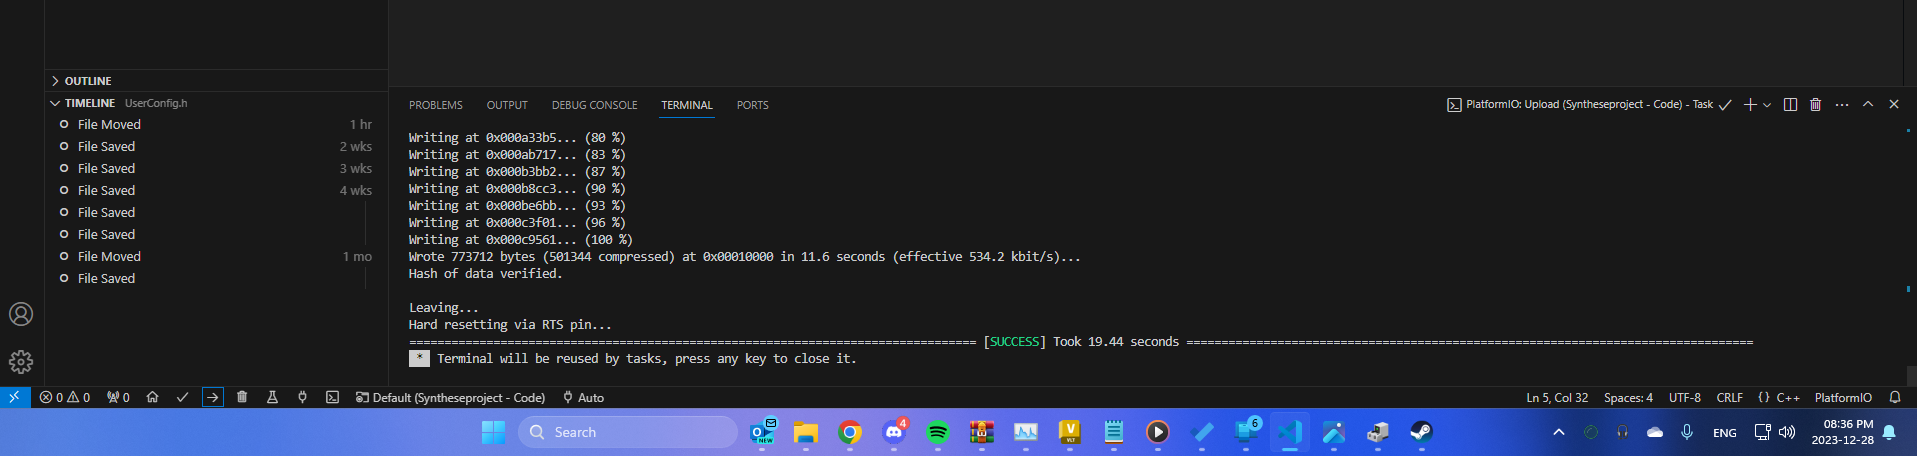
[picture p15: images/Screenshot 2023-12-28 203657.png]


## Stap 19: Batterijen plaatsen
Nu is alles klaar om de robot zijn eigen voeding te geven. Verbreek de verbinding met de PC en haal de USB kabel eruit. Plaats de twee XTAR batterijen in de houder en zet de switch in de ON positie.



## Stap 20: Robot starten
Maak verbinding met de robot en geef de stabiele waardes in. Meet uitleg hierover kan u vinden in de [manual.](../gebruiksaanwijzing/readme.md) Druk vervolgens op de startknop, vanaf nu kan je de waardes aanpassen om zoveel mogelijk snelheid te halen. Veel succes!



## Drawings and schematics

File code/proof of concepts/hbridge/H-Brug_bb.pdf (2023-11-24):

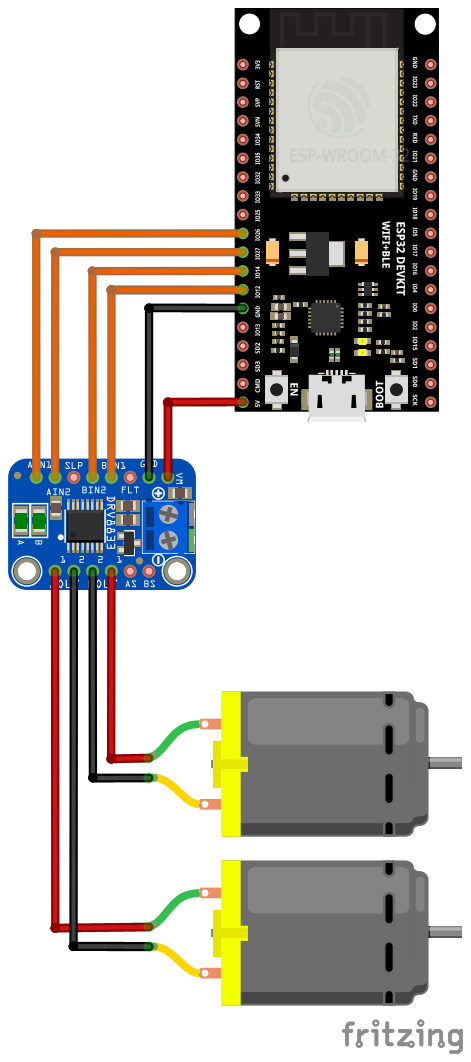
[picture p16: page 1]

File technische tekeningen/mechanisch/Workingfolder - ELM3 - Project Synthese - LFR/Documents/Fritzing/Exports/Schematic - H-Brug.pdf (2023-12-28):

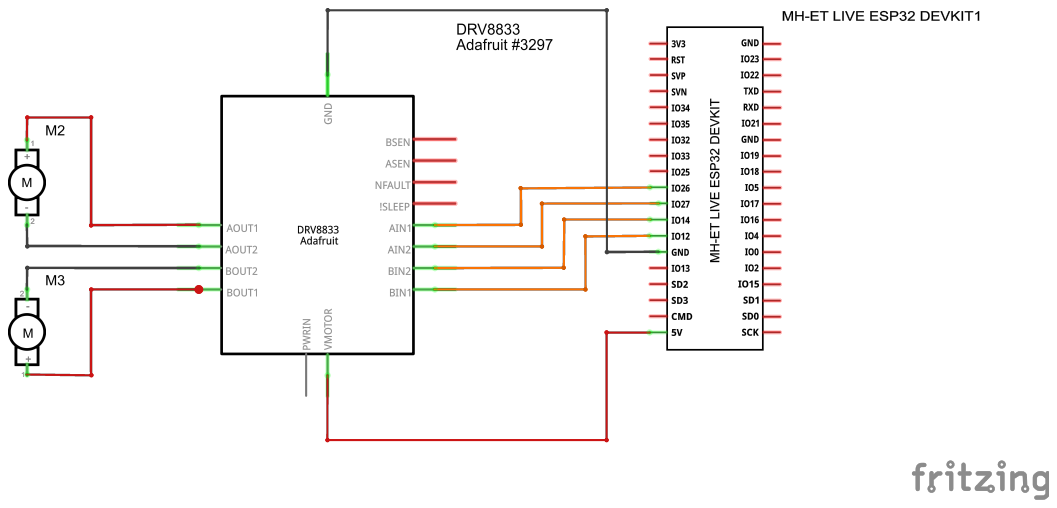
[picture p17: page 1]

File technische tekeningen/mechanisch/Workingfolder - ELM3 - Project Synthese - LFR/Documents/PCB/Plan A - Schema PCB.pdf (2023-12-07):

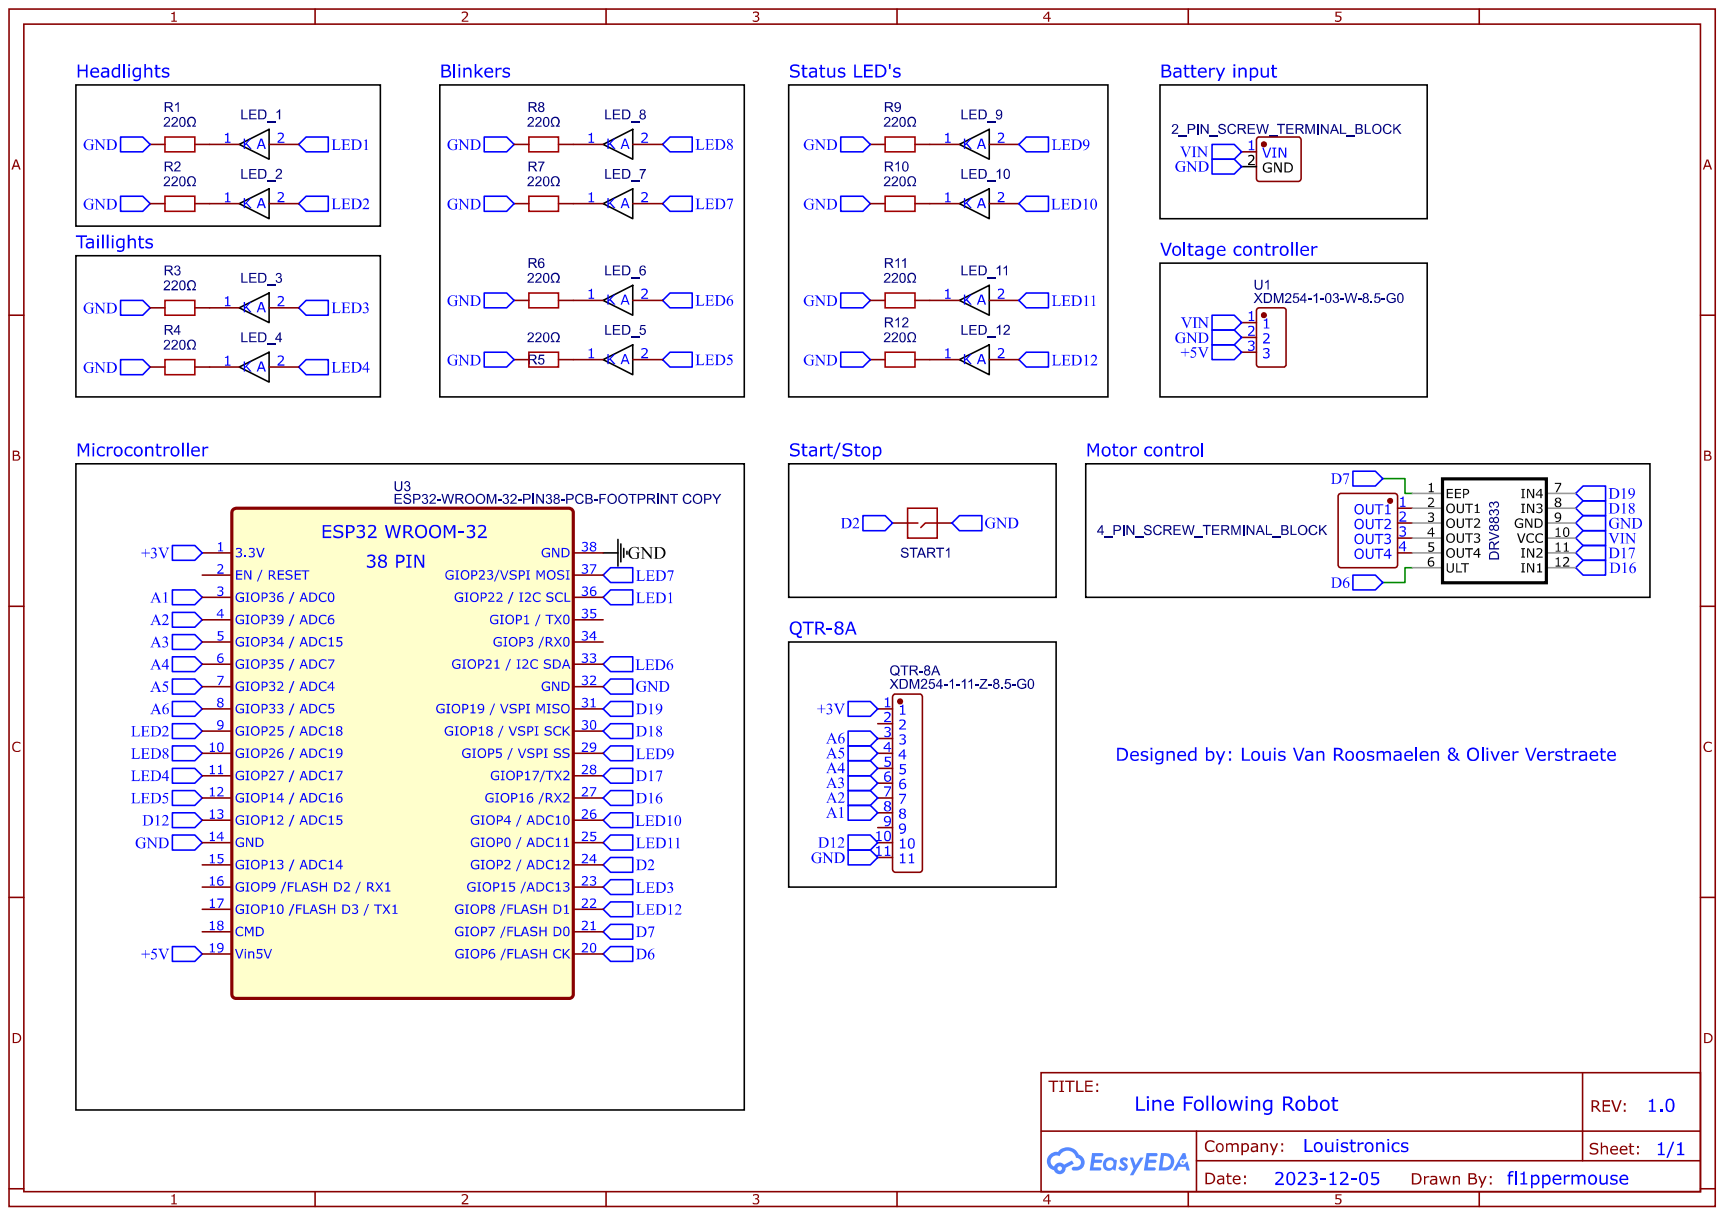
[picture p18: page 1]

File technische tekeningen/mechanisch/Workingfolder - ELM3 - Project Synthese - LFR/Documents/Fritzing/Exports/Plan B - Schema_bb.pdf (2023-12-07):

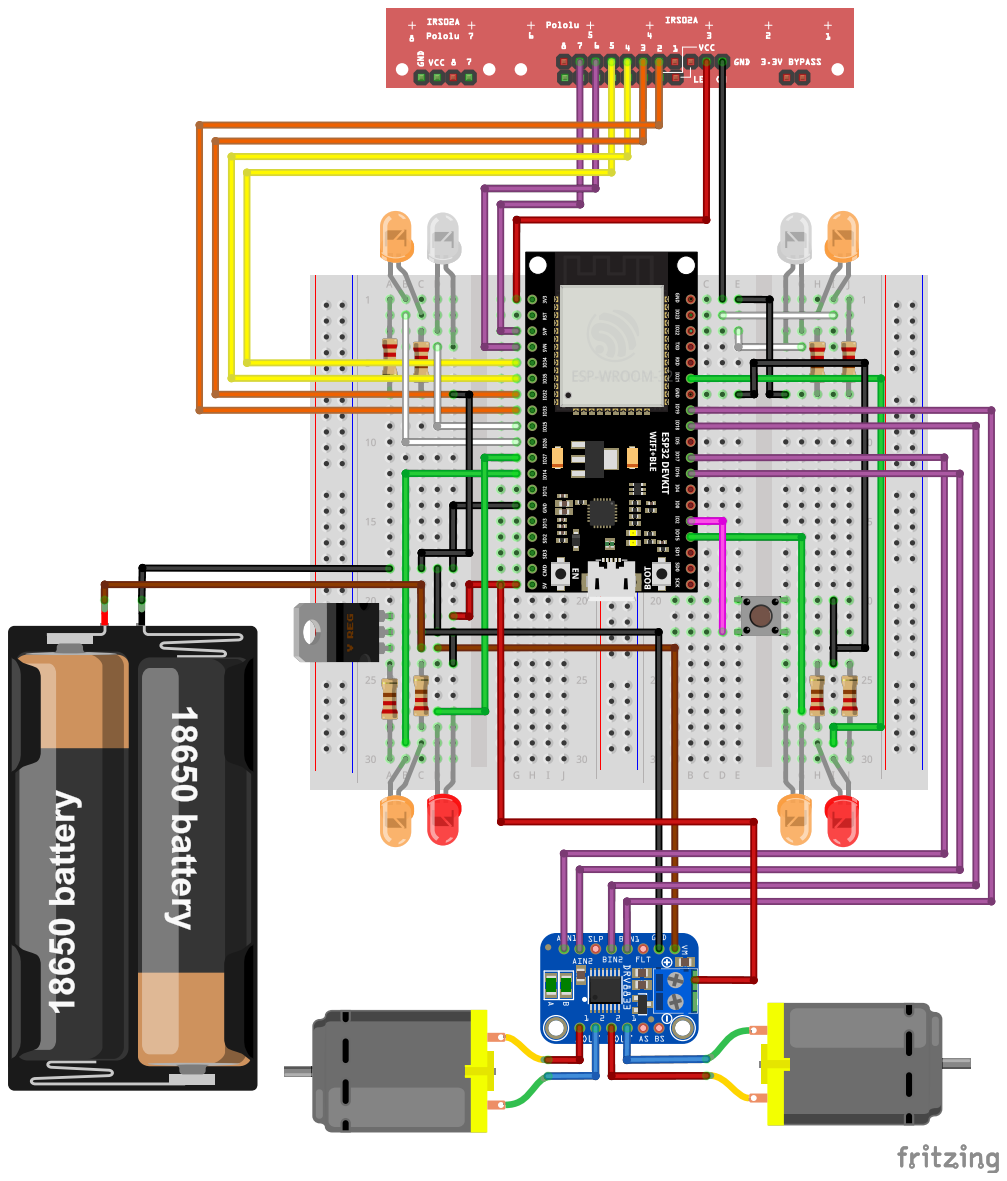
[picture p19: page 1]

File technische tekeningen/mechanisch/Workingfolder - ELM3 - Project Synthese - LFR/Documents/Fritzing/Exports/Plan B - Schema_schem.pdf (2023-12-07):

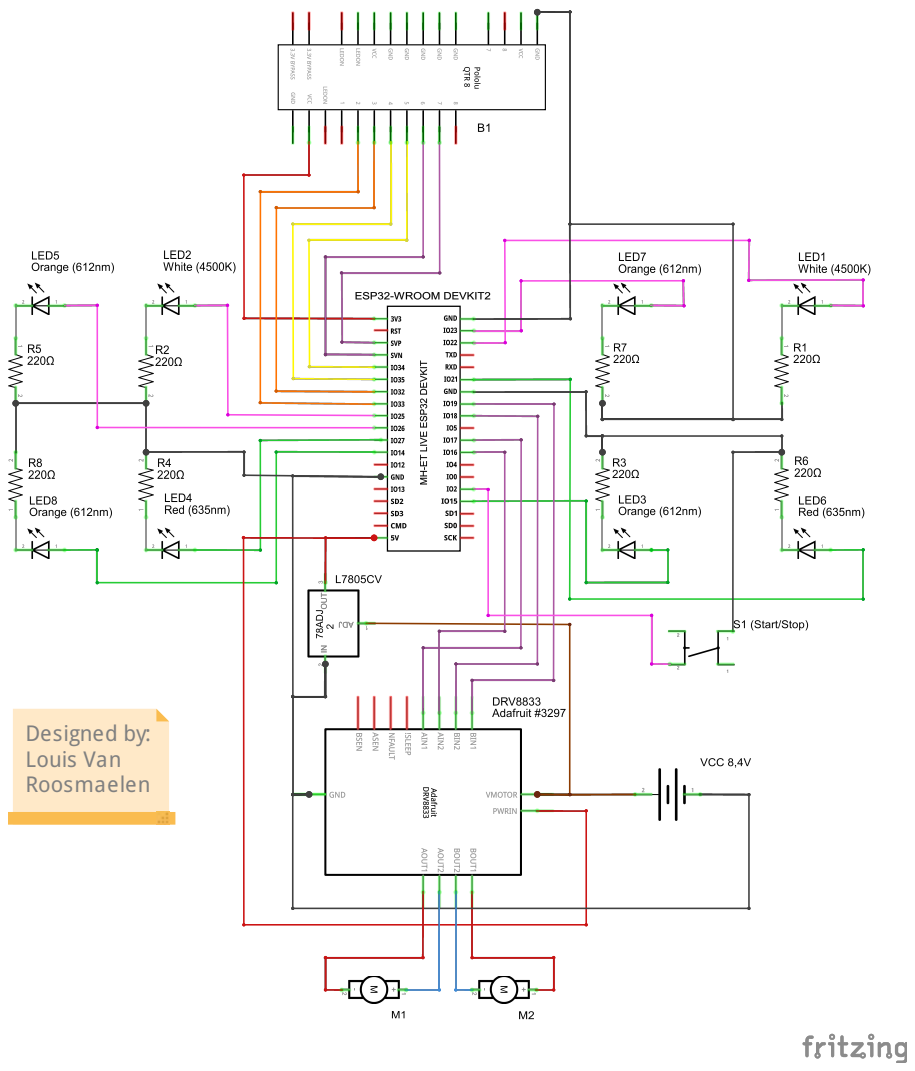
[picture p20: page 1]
Designed by: Louis Van Roosmaelen

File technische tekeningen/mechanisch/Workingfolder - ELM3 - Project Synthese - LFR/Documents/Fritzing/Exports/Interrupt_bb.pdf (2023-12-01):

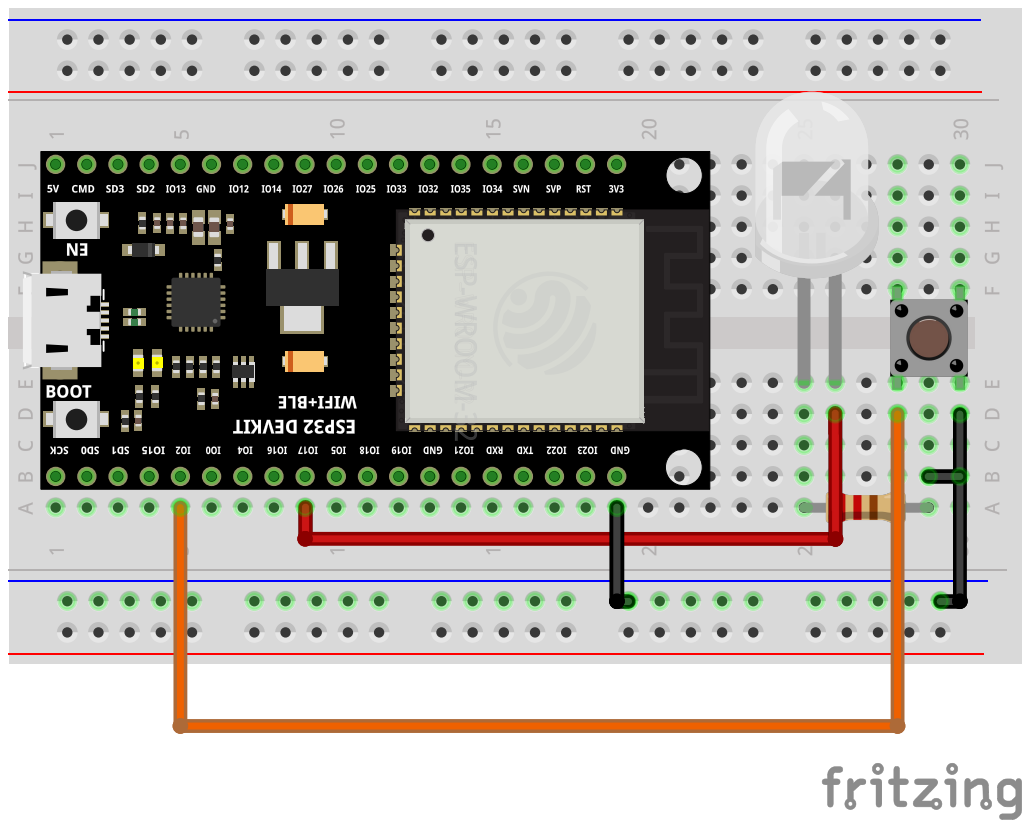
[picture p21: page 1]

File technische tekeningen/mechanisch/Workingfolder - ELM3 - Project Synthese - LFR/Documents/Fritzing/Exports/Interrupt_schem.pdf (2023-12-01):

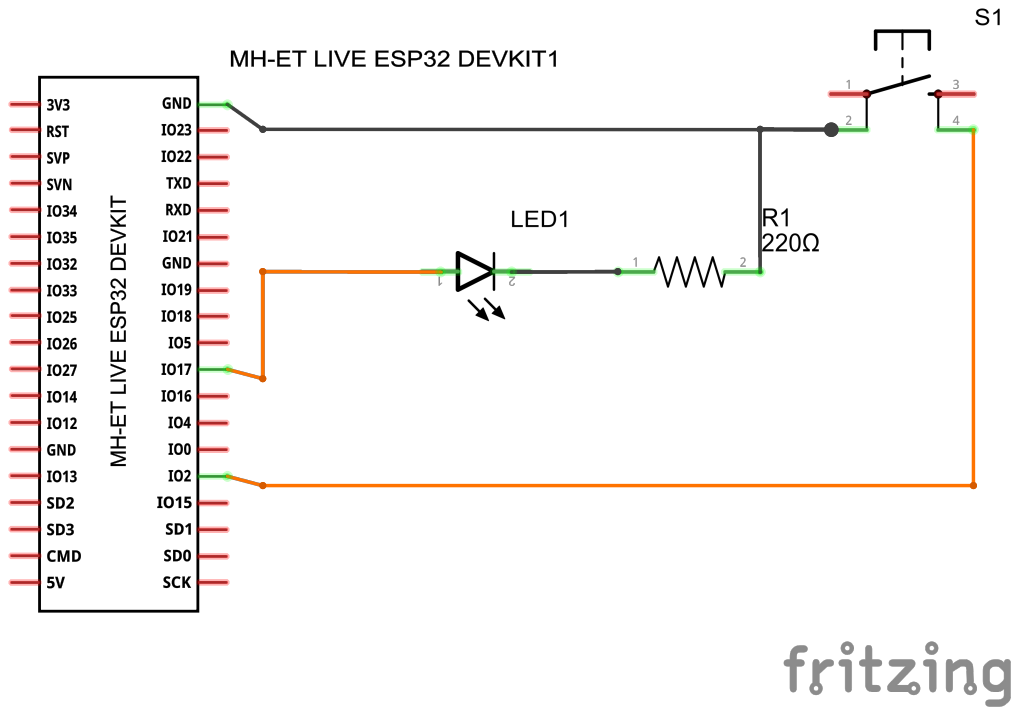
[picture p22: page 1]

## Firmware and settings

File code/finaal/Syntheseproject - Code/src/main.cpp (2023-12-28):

#include <Arduino.h>
#include <WiFi.h>
#include <EEPROM.h>
#include "TelnetCommand.h"
#include "TelnetCommand.cpp"
#include "StreamCommand.h"
#include "StreamCommand.cpp"
#include "UserConfig.h"

#define SerialPort Serial
#define Baudrate 115200
#define motor1PWM1 16
#define motor1PWM2 17
#define motor2PWM1 18
#define motor2PWM2 19

int telnetPort = 2121;
int sensors[] = {36, 39, 34, 35, 32, 33};
int normalised[6];
float iTerm = 0;
float lastError = 0;
float debugPosition;
const int ledRed[] = {15, 27};
const int ledWhite[] = {22, 25};
const int ledOrangeLeft[] = {14, 26};
const int ledOrangeRight[] = {23, 21};
const int ledStatusBlue = 5;
const int ledStatusGreen = 4;
const int ledStatusOrange = 0;
const int ledStatusRed = 12; 
const int buttonToggleState = 2;
unsigned long previous;
unsigned long calculationTime;
volatile bool running = false;

void unknownCommand(char *command);
void handleTelnet();
void onRunCommand();
void onDebug();
void onSetTelnet();
void onSetStream();
void onCalibrateTelnet();
void onCalibrateStream();
void standby();
void buttonInterrupt();
void offTrack();

WiFiServer telnetServer(telnetPort);
WiFiClient telnetClient;
TelnetCommand telnetCommand(SerialPort);
StreamCommand streamCommand(SerialPort);

struct param_t 
{
  unsigned long cycleTime;
  int blacks[6];
  int whites[6];
  int power;
  int brightnessRed;
  int brightnessWhite;
  int brightnessOrange;
  int brightnessStatus;
  int blinkLimit;
  float diff;
  float kp;
  float ki;
  float kd;
} params;
#define EEPROM_SIZE sizeof(param_t)

void setup() 
{
  digitalWrite(5, LOW);
  digitalWrite(4, LOW);
  digitalWrite(0, LOW);
  digitalWrite(12, LOW);

  pinMode(ledStatusBlue, OUTPUT);
  pinMode(ledStatusGreen, OUTPUT);
  pinMode(ledStatusOrange, OUTPUT);
  pinMode(ledStatusRed, OUTPUT);
  pinMode(buttonToggleState, INPUT_PULLUP);
  attachInterrupt(digitalPinToInterrupt(buttonToggleState), buttonInterrupt, FALLING);
  for (int i = 0; i < sizeof(ledRed) / sizeof(ledRed[0]); ++i) {pinMode(ledRed[i], OUTPUT);}
  for (int i = 0; i < sizeof(ledWhite) / sizeof(ledWhite[0]); ++i) {pinMode(ledWhite[i], OUTPUT);}
  for (int i = 0; i < sizeof(ledOrangeLeft) / sizeof(ledOrangeLeft[0]); ++i) {pinMode(ledOrangeLeft[i], OUTPUT);}
  for (int i = 0; i < sizeof(ledOrangeRight) / sizeof(ledOrangeRight[0]); ++i) {pinMode(ledOrangeRight[i], OUTPUT);}

  SerialPort.begin(Baudrate);
  WiFi.setHostname(host);
  WiFi.begin(ssid, pswd);
  while (WiFi.status() != WL_CONNECTED) 
  {
    SerialPort.println("Connecting to WiFi...");
    analogWrite(ledStatusBlue, 100);
    delay(1000);
    analogWrite(ledStatusBlue, 0);
    delay(1000);
  }
  SerialPort.println("Connected to WiFi");
  SerialPort.print("IP address: ");
  SerialPort.println(WiFi.localIP());
  analogWrite(ledStatusBlue, 100);

  telnetServer.begin();
  SerialPort.print("Telnet server started on port ");
  SerialPort.println(telnetPort);

  telnetCommand.addCommand("run", onRunCommand);
  telnetCommand.addCommand("debug", onDebug);
  telnetCommand.addCommand("set", onSetTelnet);
  telnetCommand.addCommand("calibrate", onCalibrateTelnet);
  telnetCommand.setDefaultHandler(unknownCommand);

  streamCommand.addCommand("run", onRunCommand);
  streamCommand.addCommand("debug", onDebug);
  streamCommand.addCommand("set", onSetStream);
  streamCommand.addCommand("calibrate", onCalibrateStream);
  streamCommand.setDefaultHandler(unknownCommand);

  EEPROM.begin(EEPROM_SIZE);
  EEPROM.get(0, params);
  EEPROM.end();

  analogWrite(ledStatusGreen, params.brightnessStatus);
}

void loop() 
{
  handleTelnet();
  streamCommand.readStream();
  unsigned long current = micros();

  if (current - previous >= params.cycleTime) 
  {  
    previous = current;
    //Sensorwaardes normaliseren
    for (int i = 0; i < 6; ++i) {normalised[i] = map(analogRead(sensors[i]), params.blacks[i], params.whites[i], 0, 4096);}
    
    //Starten van positie berekening
    int index = 0;
    float position;
    for (int i = 1; i < 6; i++) {if (normalised[i] < normalised[index]) {index = i;}} 

    if ((normalised[index] > 3500) && (running == true)) {running = false; analogWrite(ledStatusRed, params.brightnessStatus);}

    //Positieberekening in ongeveer mm omzetten
    if (index == 0) {position = -30;}
    else if (index == 5) {position = 30;}
    else 
    {
      int sNul = normalised[index];
      int sMinEen = normalised[index -1];
      int sPlusEen = normalised[index +1];

      float b = sPlusEen - sMinEen;
      b = b / 2;      
      float a = sPlusEen - b - sNul;
      position = -b / (2 * a);
      position += index;
      position -= 2.5;
      position *= 15;
    }
    debugPosition = position;

    //Proportioneele regelaar
    float error = -position;
    float output = error * params.kp;

    //Integrerende regelaar
    iTerm += params.ki * error;
    iTerm = constrain(iTerm, -510, 510);
    output += iTerm;

    //Differentierend regelen
    output += params.kd * (error - lastError);
    lastError = error; 

    //Aansturen van de motoren
    output = constrain(output, -510, 510);
    int powerLeft = 0;
    int powerRight = 0;

    if (running) 
    {
      if (output >= 0) 
      {
        powerLeft = constrain(params.power + params.diff * output, -255, 255);
        powerRight = constrain(powerLeft - output, -255, 255);
        powerLeft = powerRight + output;
      }  
      else 
      {
        powerRight = constrain(params.power - params.diff * output, -255, 255);
        powerLeft = constrain(powerRight + output, -255, 255);
        powerRight = powerLeft - output;
      }

      if (position > params.blinkLimit) 
      {
        for (int i = 0; i < sizeof(ledOrangeLeft) / sizeof(ledOrangeLeft[0]); ++i)  {analogWrite(ledOrangeLeft[i], params.brightnessOrange);}
        for (int i = 0; i < sizeof(ledOrangeRight) / sizeof(ledOrangeRight[0]); ++i)  {analogWrite(ledOrangeRight[i], 0);}
      }
      else if (position < -(params.blinkLimit)) 
      {
        for (int i = 0; i < sizeof(ledOrangeRight) / sizeof(ledOrangeRight[0]); ++i)  {analogWrite(ledOrangeRight[i], params.brightnessOrange);}
        for (int i = 0; i < sizeof(ledOrangeLeft) / sizeof(ledOrangeLeft[0]); ++i)  {analogWrite(ledOrangeLeft[i], 0);}
      }
      else 
      {
        for (int i = 0; i < sizeof(ledOrangeRight) / sizeof(ledOrangeRight[0]); ++i)  {analogWrite(ledOrangeRight[i], 0);}
        for (int i = 0; i < sizeof(ledOrangeLeft) / sizeof(ledOrangeLeft[0]); ++i)  {analogWrite(ledOrangeLeft[i], 0);}
      }

      analogWrite(motor1PWM1, powerLeft > 0 ? powerLeft : 0);
      analogWrite(motor1PWM2, powerLeft < 0 ? -powerLeft : 0);
      analogWrite(motor2PWM1, powerRight > 0 ? powerRight : 0);
      analogWrite(motor2PWM2, powerRight < 0 ? -powerRight : 0);
    }
    else {standby();}
  }

  unsigned long difference = micros() - current;
  if (difference > calculationTime) calculationTime = difference;
}

void handleTelnet() 
{
  if (telnetServer.hasClient()) 
  {
    if (!telnetClient || !telnetClient.connected()) 
    {
      if (telnetClient) {telnetClient.stop();}
      telnetClient = telnetServer.available();
      if (telnetClient) 
      {
        Serial.println("New Telnet client connected");
        telnetClient.println("Welcome to ESP32 - Line follower Telnet Server");
      }
    }
  }

  if (telnetClient && telnetClient.connected() && telnetClient.available()) 
  {
    telnetCommand.readStream(telnetClient);
  }
  if (telnetClient && !telnetClient.connected()) 
  {
    Serial.println("Telnet client disconnected");
    telnetClient.stop();
    analogWrite(ledStatusBlue, 0);
  }
}

void unknownCommand(char *command)
{
  Serial.print("Unknown command: ");
  Serial.println(command);
  telnetClient.print("Unknown command: ");
  telnetClient.println(command);
}

void onSetStream()
{
  char* param = streamCommand.next();
  char* value = streamCommand.next();

  SerialPort.print("Received param: ");
  SerialPort.println(param);
  SerialPort.print("Received value: ");
  SerialPort.println(value);   
  
  if (strcmp(param, "cycle") == 0) 
  {
    long newCycleTime = atol(value);
    float ratio = ((float) newCycleTime) / ((float) params.cycleTime);
    params.ki *= ratio;
    params.kd /= ratio;
    params.cycleTime = newCycleTime;
    SerialPort.print("New cycle time: ");
    SerialPort.println(params.cycleTime);
  }
  else if (strcmp(param, "ki") == 0) 
  {
    float cycleTimeInSec = ((float) params.cycleTime) / 1000000;
    params.ki = atof(value) * cycleTimeInSec;
    SerialPort.print("New ki value: ");
    SerialPort.println(params.ki);
  }
  else if (strcmp(param, "kd") == 0) 
  {
    float cycleTimeInSec = ((float) params.cycleTime) / 1000000;
    params.kd = atof(value) / cycleTimeInSec;
    SerialPort.print("New kd value: ");
    SerialPort.println(params.kd);
  }
  else if (strcmp(param, "power") == 0) 
  {
    params.power = atol(value);
    SerialPort.print("New power value: ");
    SerialPort.println(params.power);
  }
  else if (strcmp(param, "diff") == 0)
  {
    params.diff = atol(value);
    SerialPort.print("New diff value: ");
    SerialPort.println(params.diff);
  }
  else if (strcmp(param, "kp") == 0)
  {
    params.kp = atol(value);
    SerialPort.print("New kp value: ");
    SerialPort.println(params.kp);
  }
  else if (strcmp(param, "ledred") == 0)
  {
    params.brightnessRed = atol(value);
    for (int i = 0; i < sizeof(ledRed) / sizeof(ledRed[0]); ++i) {analogWrite(ledRed[i], params.brightnessRed);}
    SerialPort.print("New red led brightness: ");
    SerialPort.println(params.brightnessRed);
  }
  else if (strcmp(param, "ledwhite") == 0)
  {
    params.brightnessWhite = atol(value);
    for (int i = 0; i < sizeof(ledWhite) / sizeof(ledWhite[0]); ++i) {analogWrite(ledWhite[i], params.brightnessWhite);}
    SerialPort.print("New red led brightness: ");
    SerialPort.println(params.brightnessWhite);
  }
  else if (strcmp(param, "ledorange") == 0) 
  {
    params.brightnessOrange = atol(value);
    for (int i = 0; i < sizeof(ledOrangeLeft) / sizeof(ledOrangeLeft[0]); ++i) {analogWrite(ledOrangeLeft[i], params.brightnessOrange);}
    for (int i = 0; i < sizeof(ledOrangeRight) / sizeof(ledOrangeRight[0]); ++i) {analogWrite(ledOrangeRight[i], params.brightnessOrange);}
    SerialPort.print("New orange LED brightness: ");
    SerialPort.println(params.brightnessOrange);
  }
  else if (strcmp(param, "ledon") == 0)
  {
    for (int i = 0; i < sizeof(ledRed) / sizeof(ledRed[0]); ++i)
    {
      analogWrite(ledRed[i], params.brightnessRed);
    }
    for (int i = 0; i < sizeof(ledWhite) / sizeof(ledWhite[0]); ++i)
    {
      analogWrite(ledWhite[i], params.brightnessWhite);
    }
    SerialPort.print("Red LED's turned on, brightness: ");
    SerialPort.println(params.brightnessRed);
    SerialPort.print("White LED's turned on, brightness: ");
    SerialPort.println(params.brightnessWhite);
  }
  else if (strcmp(param, "ledoff") == 0)
  {
    for (int i = 0; i < sizeof(ledRed) / sizeof(ledRed[0]); ++i)
    {
      analogWrite(ledRed[i], 0);
    }
    for (int i = 0; i < sizeof(ledWhite) / sizeof(ledWhite[0]); ++i)
    {
      analogWrite(ledWhite[i], 0);
    }
    SerialPort.print("Red LED's turned on, brightness: ");
    SerialPort.println(params.brightnessRed);
    SerialPort.print("White LED's turned on, brightness: ");
    SerialPort.println(params.brightnessWhite);
  }
  else if (strcmp(param, "blinklimit") == 0)
  {
    params.blinkLimit = atol(value);
    SerialPort.print("New blink limit: ");
    SerialPort.println(params.blinkLimit);
  }
  else if (strcmp(param, "ledstatus") == 0)
  {
    params.brightnessStatus = atol(value);
    SerialPort.print("New status LED brightness: ");
    SerialPort.println(params.brightnessStatus);
  }
  else
  {
    SerialPort.print("Unknown command: ");
    SerialPort.println(param);
  }

  EEPROM.begin(EEPROM_SIZE);
  EEPROM.put(0, params);
  EEPROM.commit();
  EEPROM.end();
}

void onSetTelnet()
{
  char* param = telnetCommand.next();
  char* value = telnetCommand.next();

  SerialPort.print("Received param: ");
  SerialPort.println(param);
  SerialPort.print("Received value: ");
  SerialPort.println(value);   
  
  if (strcmp(param, "cycle") == 0) 
  {
    long newCycleTime = atol(value);
    float ratio = ((float) newCycleTime) / ((float) params.cycleTime);
    params.ki *= ratio;
    params.kd /= ratio;
    params.cycleTime = newCycleTime;
    telnetClient.print("New cycle time: ");
    telnetClient.println(params.cycleTime);
  }
  else if (strcmp(param, "ki") == 0) 
  {
    float cycleTimeInSec = ((float) params.cycleTime) / 1000000;
    params.ki = atof(value) * cycleTimeInSec;
    telnetClient.print("New ki value: ");
    telnetClient.println(params.ki);
  }
  else if (strcmp(param, "kd") == 0) 
  {
    float cycleTimeInSec = ((float) params.cycleTime) / 1000000;
    params.kd = atof(value) / cycleTimeInSec;
    telnetClient.print("New kd value: ");
    telnetClient.println(params.kd);
  }
  else if (strcmp(param, "power") == 0) 
  {
    params.power = atol(value);
    telnetClient.print("New power value: ");
    telnetClient.println(params.power);
  }
  else if (strcmp(param, "diff") == 0) 
  {
    params.diff = atof(value);
    telnetClient.print("New diff value: ");
    telnetClient.println(params.diff);
  }
  else if (strcmp(param, "kp") == 0) 
  {
    params.kp = atof(value);
    telnetClient.print("New kp value: ");
    telnetClient.println(params.kp);
  }
  else if (strcmp(param, "ledred") == 0)
  {
    params.brightnessRed = atol(value);
    for (int i = 0; i < sizeof(ledRed) / sizeof(ledRed[0]); ++i) {analogWrite(ledRed[i], params.brightnessRed);}
    telnetClient.print("New red led brightness: ");
    telnetClient.println(params.brightnessRed);
  }
  else if (strcmp(param, "ledwhite") == 0)
  {
    params.brightnessWhite = atol(value);
    for (int i = 0; i < sizeof(ledWhite) / sizeof(ledWhite[0]); ++i) {analogWrite(ledWhite[i], params.brightnessWhite);}
    telnetClient.print("New red led brightness: ");
    telnetClient.println(params.brightnessWhite);
  }
  else if (strcmp(param, "ledorange") == 0) 
  {
    params.brightnessOrange = atol(value);
    for (int i = 0; i < sizeof(ledOrangeLeft) / sizeof(ledOrangeLeft[0]); ++i) {analogWrite(ledOrangeLeft[i], params.brightnessOrange);}
    for (int i = 0; i < sizeof(ledOrangeRight) / sizeof(ledOrangeRight[0]); ++i) {analogWrite(ledOrangeRight[i], params.brightnessOrange);}
    telnetClient.print("New orange LED brightness: ");
    telnetClient.println(params.brightnessOrange);
  }
  else if (strcmp(param, "ledon") == 0)
  {
    for (int i = 0; i < sizeof(ledRed) / sizeof(ledRed[0]); ++i)
    {
      analogWrite(ledRed[i], params.brightnessRed);
    }
    for (int i = 0; i < sizeof(ledWhite) / sizeof(ledWhite[0]); ++i)
    {
      analogWrite(ledWhite[i], params.brightnessWhite);
    }
    telnetClient.print("Red LED's turned on, brightness: ");
    telnetClient.println(params.brightnessRed);
    telnetClient.print("White LED's turned on, brightness: ");
    telnetClient.println(params.brightnessWhite);
  }
  else if (strcmp(param, "ledoff") == 0)
  {
    for (int i = 0; i < sizeof(ledRed) / sizeof(ledRed[0]); ++i)
    {
      analogWrite(ledRed[i], 0);
    }
    for (int i = 0; i < sizeof(ledWhite) / sizeof(ledWhite[0]); ++i)
    {
      analogWrite(ledWhite[i], 0);
    }
    telnetClient.print("Red LED's turned on, brightness: ");
    telnetClient.println(params.brightnessRed);
    telnetClient.print("White LED's turned on, brightness: ");
    telnetClient.println(params.brightnessWhite);
  }
  else if (strcmp(param, "blinklimit") == 0)
  {
    params.blinkLimit = atol(value);
    telnetClient.print("New blink limit: ");
    telnetClient.println(params.blinkLimit);
  }
  else if (strcmp(param, "ledstatus") == 0)
  {
    params.brightnessStatus = atol(value);
    SerialPort.print("New status LED brightness: ");
    SerialPort.println(params.brightnessStatus);
  }
  else
  {
    Serial.print("Unknown command: ");
    Serial.println(param);
    telnetClient.print("Unknown command: ");
    telnetClient.println(param);
  }

  EEPROM.begin(EEPROM_SIZE);
  EEPROM.put(0, params);
  EEPROM.commit();
  EEPROM.end();
}

void onDebug()
{
  //SERIAL
  SerialPort.println("Cycle time: " + String(params.cycleTime));
  SerialPort.println("Calculation time: " + String(calculationTime));

  SerialPort.print("Blacks: ");
  for (int i = 0; i < 6; i++)
  {
    SerialPort.print(params.blacks[i]);
    SerialPort.print(" ");
  }
  SerialPort.println(" ");

  SerialPort.print("Whites: ");
  for (int i = 0; i < 6; i++)
  {
    SerialPort.print(params.whites[i]);
    SerialPort.print(" ");
  }
  SerialPort.println(" ");

  SerialPort.print("normalised values: ");
  for (int i = 0; i < 6; ++i) {SerialPort.print(normalised[i]); SerialPort.print(" ");}
  SerialPort.println();

  SerialPort.print("Position: ");
  SerialPort.println(debugPosition);
  SerialPort.print("Power: ");
  SerialPort.println(params.power);
  SerialPort.print("Diff: ");
  SerialPort.println(params.diff);
  SerialPort.print("Kp: ");
  SerialPort.println(params.kp);
  SerialPort.print("Brightness red: ");
  SerialPort.println(params.brightnessRed);
  SerialPort.print("Brightness white: ");
  SerialPort.println(params.brightnessWhite);
  SerialPort.print("Brightness orange: ");
  SerialPort.println(params.brightnessOrange);
  SerialPort.print("Brightness status: ");
  SerialPort.println(params.brightnessStatus);
  SerialPort.print("Blink limit: ");
  SerialPort.println(params.blinkLimit);
  
  float cycleTimeInSec = ((float) params.cycleTime) / 1000000;
  float ki = params.ki / cycleTimeInSec;
  SerialPort.print("Ki: ");
  SerialPort.println(ki);

  float kd = params.kd * cycleTimeInSec;
  SerialPort.print("Kd: ");
  SerialPort.println(kd);

  //TELNET
  telnetClient.println("Cycle time: " + String(params.cycleTime));
  telnetClient.println("Calculation time: " + String(calculationTime));

  telnetClient.print("Blacks: ");
  for (int i = 0; i < 6; i++)
  {
    telnetClient.print(params.blacks[i]);
    telnetClient.print(" ");
  }
  telnetClient.println(" ");

  telnetClient.print("Whites: ");
  for (int i = 0; i < 6; i++)
  {
    telnetClient.print(params.whites[i]);
    telnetClient.print(" ");
  }
  telnetClient.println(" ");

  telnetClient.print("normalised values: ");
  for (int i = 0; i < 6; ++i) {telnetClient.print(normalised[i]); telnetClient.print(" ");}
  telnetClient.println();

  telnetClient.print("Position: ");
  telnetClient.println(debugPosition);
  telnetClient.print("Power: ");
  telnetClient.println(params.power);
  telnetClient.print("Diff: ");
  telnetClient.println(params.diff);
  telnetClient.print("Kp: ");
  telnetClient.println(params.kp);
  telnetClient.print("Ki: ");
  telnetClient.println(ki);
  telnetClient.print("Kd: ");
  telnetClient.println(kd);
  telnetClient.print("Brightness red: ");
  telnetClient.println(params.brightnessRed);
  telnetClient.print("Brightness white: ");
  telnetClient.println(params.brightnessWhite);
  telnetClient.print("Brightness orange: ");
  telnetClient.println(params.brightnessOrange);
  telnetClient.print("Brightness status: ");
  telnetClient.println(params.brightnessStatus);
  telnetClient.print("Blink limit: ");
  telnetClient.println(params.blinkLimit);
}

void onCalibrateStream()
{
  char* param = streamCommand.next();

  if (strcmp(param, "black") == 0)
  {
    SerialPort.println("Calibrating blacks... ");
    for (int i = 0; i < 6; i++)
    {
      params.blacks[i]=analogRead(sensors[i]);
      SerialPort.print("Sensor");
      SerialPort.print(i);
      SerialPort.print(" : ");
      SerialPort.println(params.blacks[i]);
    } 
    SerialPort.println("Done.");
    SerialPort.println();
  }
  else if (strcmp(param, "white") == 0)
  {
    SerialPort.println("Calibrating whites... ");
    for (int i = 0; i < 6; i++) 
    {
      params.whites[i]=analogRead(sensors[i]);
      SerialPort.print("Sensor");
      SerialPort.print(i);
      SerialPort.print(" : ");
      SerialPort.println(params.whites[i]);
    }  
    SerialPort.println("Done.");
    SerialPort.println();
  }

  EEPROM.begin(EEPROM_SIZE);
  EEPROM.put(0, params);
  EEPROM.commit();
  EEPROM.end();
}

void onCalibrateTelnet()
{
  char* param = telnetCommand.next();

  if (strcmp(param, "black") == 0)
  {
    telnetClient.print("start calibrating black... ");
    telnetClient.print("start calibrating black... ");
    for (int i = 0; i < 6; i++) params.blacks[i]=analogRead(sensors[i]);
    telnetClient.println("done");
    telnetClient.println("done");
  }
  else if (strcmp(param, "white") == 0)
  {
    telnetClient.print("start calibrating white... ");
    telnetClient.print("start calibrating white... ");    
    for (int i = 0; i < 6; i++) params.whites[i]=analogRead(sensors[i]);  
    telnetClient.println("done");
    telnetClient.println("done");      
  }

  EEPROM.begin(EEPROM_SIZE);
  EEPROM.put(0, params);
  EEPROM.commit();
  EEPROM.end();
}

void onRunCommand()
{
  if (running == true)  
  {
    running = false;
    telnetClient.println("Robot set to standby");
  }
  else              
  {
    for (int i = 0; i < sizeof(ledOrangeLeft) / sizeof(ledOrangeLeft[0]); ++i) {analogWrite(ledOrangeLeft[i], 0);}
    for (int i = 0; i < sizeof(ledOrangeRight) / sizeof(ledOrangeRight[0]); ++i) {analogWrite(ledOrangeRight[i], 0);}
    analogWrite(ledStatusRed, 0);
    running = true;
    telnetClient.println("Robot set to run");
  }
}
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
